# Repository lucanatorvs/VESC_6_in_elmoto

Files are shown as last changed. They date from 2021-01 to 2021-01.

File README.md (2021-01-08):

# VESC_6_in_elmoto
A electronics refit project for a electric moped

## Overall design

The dashboard contains a micro controller which is both responsible for driving
the LCD screen, and for communicating the state of the light switches to the
second dairy micro controller under the seat. There are four switches connected
to the dashboard, one for each brake lever and one for the horn and the light
switch. The VESC communicates things like battery voltige and motor rpm to the
dashboard which displays the data in a human readable format on the lcd.
The second dairy microcontroller drives realise which switch on and off the
lights and the horn.

### LCD

The LCD has a polarizing filter built in because of the operation of a LCD,
this polarization however interferes with the polarization of my sunglasses. So
I added a "depolarization filter" to the front of the LCD in the form of
waterproofing the housing.

## thermal design
The aluminium housing of the VESC6 screwed directly to the metal frame of the
scooter in place of the old ESC, with a layer of thermal interface material in
between. Due to the higher efficiency of the new ESC I don't foresee any
thermal constraints.

The heat producing components of the VESC6 are thermally connected to the
aluminium housing. There is a slight inefficiency in his flow because of this
aluminium intermediary, Theoretically the aluminium housing could be removed
and the components mounted directly to the frame, but I see no practical way of
doing this easily.

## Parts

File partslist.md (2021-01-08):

# parts list

## Elmoto hr1

This is the moped on witch the entire project is based, the only parts i used form the original are:

1. the frame and wheels (including the brakes).
2. the hub motor.
3. the battery (see below for elaboration).

### Battery

The battery can be sourced elsewhere, I recommend at least a 10s battery (but
this depends on the kind of motor you use) with at least about a kWh of
capacity, depending on your use case.

The battery that comes with the L motor is a 13S 14P I believe.

## ESC

The ESCS a VESC 6 MkV from
[trampaboards](https://trampaboards.com/1-x-vesc-6-mkv--170-tax-each-p-27529.html),
VESC is a open source project by [Benjamin
Vedder](https://github.com/vedderb/bldc-hardware). I chose this ESC Because
it's open source and powerful.  It's rating of 60V 100A comes down to a power
consumption of 6 kW. And since the maximum allowed power level in the
Netherlands is half that, the VESCS sufficiently powerful.

## Other components

I used some arduinos, perfboards, and a LCD display from
[grove](https://www.kiwi-electronics.nl/grove-lcd-rgb-backlight?search=lcd&description=true).

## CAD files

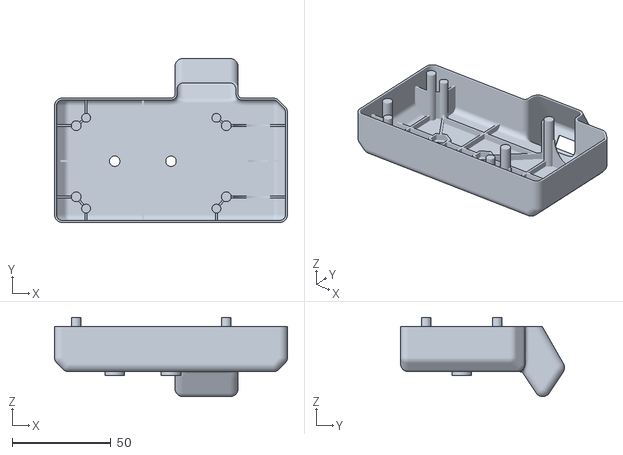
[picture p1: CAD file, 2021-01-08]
3d_design/head_unit/case.stl
118.0 x 83.0 x 40.1

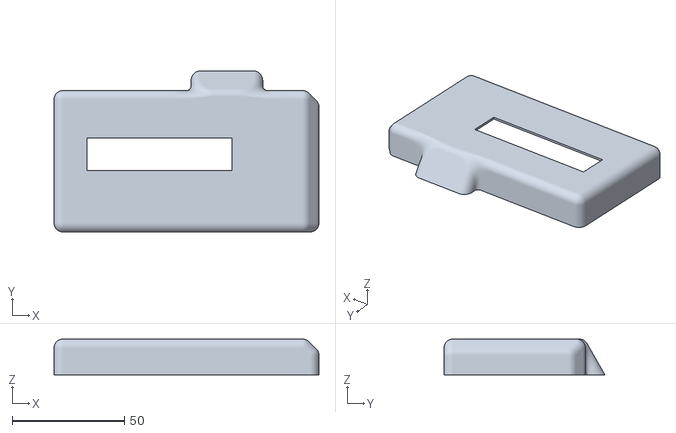
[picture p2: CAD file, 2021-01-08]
3d_design/head_unit/lid.stl
118.0 x 71.7 x 16.0

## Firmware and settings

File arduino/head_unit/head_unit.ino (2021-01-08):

/**
   Author:          Luca van Straaten (based in part on the VESC_LCD_EBIKE project by Tom Stanton)
   Created:         22.09.2020
   Compiler:        Arduino 1.8.12
   ISO/IEC 14882:   arduino c
   File:            head_unit.ino
   discription:     a control system for the head unit of a eBike
**/

#include <SoftwareSerial.h>

#include <VescUart.h>
#include <SimpleKalmanFilter.h>

//Library for the Display
#include <Wire.h>
#include "rgb_lcd.h"

rgb_lcd lcd;

/** Initiate VescUart class */
VescUart UART;

int rpm;
float voltage;
float current;
int power;
float amphour;
float tach;
float distance;
float velocity;
float watthour;
float batpercentage;

SimpleKalmanFilter Filter1(2, 2, 0.01);

SoftwareSerial softSerial(10, 11); // RX, TXe

////////// switches //////////

const int Lbrake = 3;
const int Rbrake = 4;
const int light = 5;
const int horn = 2;

bool lastlight = LOW;

float powerfiltered;


////////// Custom Characters //////////
byte ph[] = {
  B11100,
  B10100,
  B11100,
  B10000,
  B10101,
  B00111,
  B00101,
  B00101
};

byte mi[] = {
  B10001,
  B11011,
  B10101,
  B10001,
  B00100,
  B00000,
  B00100,
  B00110
};

byte km[] = {
  B01000,
  B01010,
  B01100,
  B01010,
  B10001,
  B11011,
  B10101,
  B10001
};


byte ah[] = {
  B00100,
  B01010,
  B01110,
  B01010,
  B00000,
  B01010,
  B01110,
  B01010
};
byte percent[] = {
  B11001,
  B11001,
  B00010,
  B00100,
  B01000,
  B10011,
  B10011,
  B00000
};

byte m[] = {
  B10001,
  B11011,
  B10101,
  B10001,
  B10001,
  B00000,
  B00000,
  B00000
};

byte k[] = {
  B01000,
  B01010,
  B01100,
  B01010,
  B01010,
  B00000,
  B00000,
  B00000
};

byte bat[] = {
  B01110,
  B11011,
  B10001,
  B10001,
  B10001,
  B11111,
  B11111,
  B11111
};

byte sprk[] = {
  B00000,
  B01000,
  B00100,
  B00010,
  B00100,
  B01000,
  B00100,
  B00010
};

boolean array_cmp(char *a, char *b, int len_a, int len_b) {
  int n;

  // if their lengths are different, return false
  if (len_a != len_b) return false;

  // test each element to be the same. if not, return false
  for (n = 0; n < len_a; n++) if (a[n] != b[n]) return false;

  //ok, if we have not returned yet, they are equal :)
  return true;
}

void getdataandwritetolcd () {
  ////////// Filter //////////
  // calculate the estimated value with Kalman Filter
  powerfiltered = Filter1.updateEstimate(power);

  ////////// Read values //////////
  if ( UART.getVescValues() ) {

    rpm = (UART.data.rpm) / 27;        // The '27' is the number of pole pairs in the motor.
    voltage = (UART.data.inpVoltage);
    current = (UART.data.avgInputCurrent);
    power = voltage * current;
    amphour = (UART.data.ampHours);
    watthour = amphour * voltage;
    tach = (UART.data.tachometerAbs) / 162;        // The '162' is the number of motor poles multiplied by 3
    distance = ((tach * 3.142) / 1000) * 0.64; // (Motor RPM x Pi) / meters in a  km) x Wheel diameter
    velocity = ((rpm * 3.142 * 60) / 1000) * 0.64; // ((Motor RPM x Pi x seconds in a minute) / meters in a km) x Wheel diameter
    batpercentage = ((voltage - 42) / 13) * 100;    // ((Battery voltage - minimum voltage) / number of cells) x 100


    if (velocity < 0.5 && velocity > -0.5) {
      velocity = 0;
    }

    ////////// LCD //////////

    // First line
    if (velocity < 10 && velocity >= 0) {
      lcd.setCursor(0, 0);
      lcd.print("  ");
      lcd.print(velocity, 0);
    }
    else if (velocity < 100 && velocity >= 10 || velocity > -10 && velocity < 0) {
      lcd.setCursor(0, 0);
      lcd.print(" ");
      lcd.print(velocity, 0);
    }
    else if (velocity < 10 && velocity >= 0 || velocity > -100 && velocity <= 10) {
      lcd.setCursor(0, 0);
      lcd.print(velocity, 0);
    }
    lcd.createChar(3, k);          // Change 'm' to 'k' for kilometers
    lcd.setCursor(3, 0);
    lcd.write(3);
    lcd.createChar(4, ph);
    lcd.setCursor(4, 0);
    lcd.write(4);

    lcd.setCursor(7, 0);
    lcd.print(voltage, 0);
    lcd.setCursor(9, 0);
    lcd.print("V");

    lcd.setCursor(11, 0);
    lcd.print(distance, 2);
    lcd.createChar(5, km);          // Change 'mi' to 'km' for kilometers
    lcd.setCursor(15, 0);
    lcd.write(5);

    // Second line
    if (powerfiltered < 10 && powerfiltered >= 0) {
      lcd.setCursor(0, 1);
      lcd.print("   ");
      lcd.print(powerfiltered, 0);
    }
    else if (powerfiltered >= 10 && powerfiltered < 100 || powerfiltered > -10 && powerfiltered < 0) {
      lcd.setCursor(0, 1);
      lcd.print("  ");
      lcd.print(powerfiltered, 0);
    }
    else if (powerfiltered >= 100 && powerfiltered < 1000 || powerfiltered > -100 && powerfiltered <= -10) {
      lcd.setCursor(0, 1);
      lcd.print(" ");
      lcd.print(powerfiltered, 0);
    }
    else if (powerfiltered >= 1000 || powerfiltered > -1000 && powerfiltered <= -100) {
      lcd.setCursor(0, 1);
      lcd.print(powerfiltered, 0);
    }

    lcd.setCursor(4, 1);
    lcd.print("W");

    if (batpercentage < 100) {
      lcd.setCursor(7, 1);
      lcd.print(batpercentage, 0);
    }
    else {
      lcd.setCursor(6, 1);
      lcd.print(batpercentage, 0);
    }
    lcd.createChar(6, percent);
    lcd.setCursor(9, 1);
    lcd.write(6);

    lcd.setCursor(11, 1);
    lcd.print(amphour, 2);
    lcd.createChar(7, ah);
    lcd.setCursor(15, 1);
    lcd.write(7);

    lcd.println();

  }
  else {
    lcd.println("Failed to get data!");
  }
}





void setup() {

  // set up the LCD's number of columns and rows:
  lcd.begin(16, 2);

  lcd.setCursor(3, 0);
  lcd.print("LUCA EBIKE");          // Startup screen (can't be more than 10 characters)
  lcd.createChar(1, bat);
  lcd.setCursor(1, 1);
  lcd.write(1);
  lcd.setCursor(14, 1);
  lcd.write(1);
  lcd.createChar(2, sprk);
  lcd.setCursor(1, 0);
  lcd.write(2);
  lcd.setCursor(14, 0);
  lcd.write(2);

  pinMode(Lbrake, INPUT);
  pinMode(Rbrake, INPUT);
  pinMode(light, INPUT_PULLUP);
  pinMode(horn, INPUT_PULLUP);

  /** Setup Serial port to display data */
  Serial.begin(115200);

  /** Setup UART port */
  softSerial.begin(9600);

  while (!Serial) {
    ;
  }

  /** Define which ports to use as UART */
  UART.setSerialPort(&Serial);

  delay(5000);
  lcd.clear();

  pinMode(LED_BUILTIN, OUTPUT);

}






long loop_timer;

int loop_counter = 0;
byte totransmit = 0;
byte latsransmit;

void loop() {
  loop_timer = millis() + 200; //5hz update rate.
  digitalWrite(LED_BUILTIN, LOW);    // turn the LED off by making the voltage LOW

  if (loop_counter >= 2) {
    loop_counter = 0;
    getdataandwritetolcd();
  }
  loop_counter++;

  // stuff to do with the buttons and the serial comunication
  bool readingLbrake = digitalRead(Lbrake);
  bool readingRbrake = digitalRead(Rbrake);
  bool readinglight = digitalRead(light);
  bool readinghorn = digitalRead(horn);

  char str[4];

  if (readingLbrake == LOW || powerfiltered < -100) {
    str[0] = 1;
  } else {
    str[0] = 0;
  }

  if (readingRbrake == LOW) {
    str[1] = 1;
  } else {
    str[1] = 0;
  }

  if (readinglight == LOW && lastlight == HIGH) {
    str[2] = 1;
  } else {
    str[2] = 0;
  }

  if (readinghorn == LOW) {
    str[3] = 1;
  } else {
    str[3] = 0;
  }

  totransmit = 0;

  for (int i = 0; i < 4; i++) {
    if (str[i] == 1) {
      bitSet(totransmit, i);
    }
  }

  //totransmit = 5;
  if (totransmit != latsransmit) {
    softSerial.write(totransmit);
    digitalWrite(LED_BUILTIN, HIGH);
    delay(20);
  }

  latsransmit = totransmit;

  lastlight = readinglight;

  delay(20);

  //while (millis() - loop_timer > 0) {
  //}
}

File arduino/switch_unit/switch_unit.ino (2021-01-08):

#include<Wire.h>
#include <SoftwareSerial.h>

const int mainerelay = 2;
const int brakelight = 6;
const int horn = 3;
const int headlight = 4;
const int taillight = 5;


bool lights = HIGH;
bool lastlight;

char str[3];

byte inbyte;


SoftwareSerial softSerial(19, 18); // RX, TX


void setup() {


  pinMode(headlight, OUTPUT);
  pinMode(taillight, OUTPUT);
  pinMode(horn, OUTPUT);
  pinMode(brakelight, OUTPUT);
  pinMode(LED_BUILTIN, OUTPUT);
  pinMode(mainerelay, OUTPUT);

  digitalWrite(horn, HIGH);
  digitalWrite(brakelight, HIGH);
  digitalWrite(headlight, HIGH);
  digitalWrite(taillight, HIGH);

  Serial.begin(9600);

  softSerial.begin(9600);
  softSerial.listen();

  delay(6000);

  digitalWrite(mainerelay, HIGH);

  for (int x = 0; x < 4; x++) {
    str[x] = 0;
  }

  Serial.println("test1");
}



long loop_timer;

void loop() {

  if (softSerial.available()) {
    inbyte = softSerial.read();
    Serial.println(inbyte);
  }

  for (int i = 0; i < 4; i++) {
    if (bitRead(inbyte, i)){
      str[i] = 1;
    }
    
  }

  // head light
  if (bitRead(inbyte, 2) == 1 && lastlight == 0) {
    lights = !lights;
  }

  digitalWrite(headlight, lights);
  digitalWrite(taillight, lights);

  lastlight = bitRead(inbyte, 2);

  // horn
  digitalWrite(horn, !bitRead(inbyte, 3));

  //brake light
  if (bitRead(inbyte, 0) || bitRead(inbyte, 1)) {
    digitalWrite(brakelight, LOW);
  } else {
    digitalWrite(brakelight, HIGH);
  }

  delay(20);
}
